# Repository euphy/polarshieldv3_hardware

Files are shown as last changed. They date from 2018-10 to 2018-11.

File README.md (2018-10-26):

View this project on [CADLAB.io](https://cadlab.io/project/1157). 

# polarshieldv3_hardware
Schematics, board and gerbers for Polarshield v3

Polarshield v3 is an aggregation board for connecting

* NodeMCU-32S
* 2x stepper drivers
* 320x240 LCD
* Touch panel
* SD card

v3.0e is the currently manufactured version that's inside recent PolargraphSD machines.

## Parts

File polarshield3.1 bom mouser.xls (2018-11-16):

POLARGRAPHSD V3.1 BOM
Mouser No | Mfr. No | Manufacturer | Customer No | Description | RoHS | Lifecycle | Order Qty. | Price (GBP) | Ext.: (GBP)
651-1770908 | 1770908 | Phoenix Contact |  | Fixed Terminal Blocks PTSM 0,5/ 4-2,5-H THR R32 | RoHS Compliant |  | 2 | £0.74 | £1.48
651-1778641 | 1778641 | Phoenix Contact |  | Pluggable Terminal Blocks PTSM 0,5/ 4-HH-2,5 THR R32 | RoHS Compliant |  | 4 | £0.695 | £2.78
651-1778858 | 1778858 | Phoenix Contact |  | Pluggable Terminal Blocks PTSM 0,5/ 4-P-2,5 | RoHS Compliant |  | 4 | £1.14 | £4.56
538-71764-0108 | 71764-0108 | Molex |  | Headers & Wire Housings RA BRKWY HEADER 8 PIN GOLD | RoHS Compliant |  | 1 | £0.97 | £0.97
710-865080345012 | 865080345012 | Wurth Electronics |  | Aluminium Electrolytic Capacitors - SMD WCAP-ASLI 16V 220uF 20% ESR=430mOhms | RoHS Compliant | New Product | 2 | £0.262 | £0.52
538-90121-0763 | 90121-0763 | Molex |  | Headers & Wire Housings 2.54MM CGRIDIII HDR 3P R/A SR SEL AU | RoHS Compliant |  | 1 | £0.595 | £0.60
863-BSS138LT1G | BSS138LT1G | ON Semiconductor |  | MOSFET 50V 200mA N-Channel | RoHS Compliant |  | 4 | £0.298 | £1.19
80-C0805C104Z3V | C0805C104Z3VACTU | KEMET |  | Multilayer Ceramic Capacitors MLCC - SMD/SMT 25volts 0.1uF Y5V -20+80% | RoHS Compliant |  | 2 | £0.076 | £0.15
652-CR0805FW1005ELF | CR0805-FW-1005ELF | Bourns |  | Thick Film Resistors - SMD Res 0805 10M 1% 125mW TC200 | RoHS Compliant By Exemption |  | 2 | £0.076 | £0.15
667-EEE-1CA101WP | EEE-1CA101WP | Panasonic |  | Aluminium Electrolytic Capacitors - SMD 100uF 16V | RoHS Compliant |  | 2 | £0.282 | £0.56
667-EXB-38V102JV | EXB-38V102JV | Panasonic |  | Resistor Networks & Arrays 1K OHM 5% | RoHS Compliant By Exemption |  | 1 | £0.092 | £0.09
667-EXB-38V103JV | EXB-38V103JV | Panasonic |  | Resistor Networks & Arrays 10K OHM 5% | RoHS Compliant By Exemption |  | 2 | £0.092 | £0.18
625-GF1A-E3 | GF1A-E3/67A | Vishay |  | Rectifiers 1.0 Amp 50 Volt | RoHS Compliant By Exemption |  | 1 | £0.329 | £0.33
720-LYR976-PS-36 | LY R976 | Osram Opto Semiconductor |  | Standard LEDs - SMD Yellow, 588nm 280mcd, 20mA | RoHS Compliant |  | 3 | £0.29 | £0.87
855-M20-7820442 | M20-7820442 | Harwin |  | Headers & Wire Housings 4 PIN SIL VERTICAL SOCKET GOLD+TIN | RoHS Compliant |  | 1 | £0.618 | £0.62
855-M20-7820842 | M20-7820842 | Harwin |  | Headers & Wire Housings 8 PIN SIL VERTICAL SOCKET GOLD+TIN | RoHS Compliant |  | 4 | £0.84 | £3.36
855-M20-7821446 | M20-7821446 | Harwin |  | Headers & Wire Housings 14 PIN SIL VERTICAL SOCKET TIN | RoHS Compliant |  | 1 | £1.10 | £1.10
855-M20-7822046 | M20-7822046 | Harwin |  | Headers & Wire Housings 20 PIN SIL VERTICAL SOCKET TIN | RoHS Compliant |  | 2 | £1.45 | £2.90
688-SKHHBY | SKHHBYA010 | ALPS |  | Tactile Switches 6.0x6.0x7.0mm 260gf | RoHS Compliant |  | 1 | £0.208 | £0.21

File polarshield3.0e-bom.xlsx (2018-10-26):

Part | Value | Device | Package | Description | MF | MPN | OC_FARNELL | OC_NEWARK | PROD_ID | SF_ID | VALUE | OPTIONAL
C1 | 100nF | C-EUC0805 | C0805 | CAPACITOR, European symbol
C2 | 100uF | CPOL-EU153CLV-0605 | 153CLV-0605 | POLARIZED CAPACITOR, European symbol
C3 | 100nF | C-EUC0805 | C0805 | CAPACITOR, European symbol
C4 | 220uF | CPOL-EU153CLV-0605 | 153CLV-0605 | POLARIZED CAPACITOR, European symbol
C5 | 100nF | C-EUC0805 | C0805 | CAPACITOR, European symbol
C6 | 220uF | CPOL-EU153CLV-0605 | 153CLV-0605 | POLARIZED CAPACITOR, European symbol
C7 | 100nF | C-EUC0805 | C0805 | CAPACITOR, European symbol
C8 | 100uF | CPOL-EU153CLV-0605 | 153CLV-0605 | POLARIZED CAPACITOR, European symbol
D1 | GF1A-E3/67A | DIODE-DO214BA | DO214BA | DIODE |  | GF1A-E3/67A
EXT_PWR |  | M02PTH | 1X02 | Standard 2-pin 0.1" header. Use with |  |  |  |  |  |  |  | OPTIONAL
JP3 | POWER_JACKPTH_LOCK | POWER_JACKPTH_LOCK | POWER_JACK_PTH_LOCK | Power Jack |  |  |  |  | CONN-08197 | PRT-00119
PWR |  | LEDCHIPLED_0805 | CHIPLED_0805 | LED
TX |  | LEDCHIPLED_0805 | CHIPLED_0805 | LED
RX |  | LEDCHIPLED_0805 | CHIPLED_0805 | LED
Q4 | BSS138 | MOSFET-NCHANNELSMD | SOT23-3 |  |  |  |  |  |  |  |  | OPTIONAL
Q5 | BSS138 | MOSFET-NCHANNELSMD | SOT23-3 |  |  |  |  |  |  |  |  | OPTIONAL
Q6 | BSS138 | MOSFET-NCHANNELSMD | SOT23-3 |  |  |  |  |  |  |  |  | OPTIONAL
Q7 | BSS138 | MOSFET-NCHANNELSMD | SOT23-3 |  |  |  |  |  |  |  |  | OPTIONAL
R1 | 1k | R-EU_M0805 | M0805 | RESISTOR, European symbol
R2 | 10k | R-EU_M0805 | M0805 | RESISTOR, European symbol
R4 | 1k | R-EU_M0805 | M0805 | RESISTOR, European symbol
R5 | 1k | R-EU_M0805 | M0805 | RESISTOR, European symbol
R8 | 1k | R-EU_M0805 | M0805 | RESISTOR, European symbol
R9 | 10k | R-EU_M0805 | M0805 | RESISTOR, European symbol
RESET | DTS-6 | DTS-6 | DTS-6 |  |  | SKHHBYA010
RN1 | 10k | 4R-NEXB38V | EXB38V | Array Chip Resistor |  |  | unknown | unknown |  |  |  | OPTIONAL
RN2 | 10k | 4R-NEXB38V | EXB38V | Array Chip Resistor |  |  | unknown | unknown |  |  |  | OPTIONAL
RN3 | 1k | 4R-NEXB38V | EXB38V | Array Chip Resistor |  |  | unknown | unknown
SERVO |  | PINHD-1X3/90 | 1X03/90 | PIN HEADER
U$2 | 2.4_TFT_SPI_TOUCH_SD | 2.4_TFT_SPI_TOUCH_SD | 2.4_TFT_SPI_TOUCH_SD
U$3 | MINI-360-MP2307 | MINI-360-MP2307 | MINI-360-MP2307
M1_CONN |  | PINHD-1X4/90 | 1X04/90 | PIN HEADER |  | 1778641
M2_CONN |  | PINHD-1X4/90 | 1X04/90 | PIN HEADER |  | 1778641
CN1 |  | DIP-BLACK-FEMALE-HEADER-VERT(8P-2.54) | H8-2.54 | 320030061 |  | F185-1108A1BSYC1 |  |  |  |  | 8p-2.54 | OPTIONAL
CN2 |  | DIP-BLACK-FEMALE-HEADER-VERT(8P-2.54) | H8-2.54 | 320030061 |  | F185-1108A1BSYC1 |  |  |  |  | 8p-2.54 | OPTIONAL
MOTOR_1 | A4988BREAKOUT | A4988BREAKOUT | A4988BREAKOUT
MOTOR_2 | A4988BREAKOUT | A4988BREAKOUT | A4988BREAKOUT
NODEMCU-32S1 | NODEMCU-32S | NODEMCU-32S | NODEMCU-32S

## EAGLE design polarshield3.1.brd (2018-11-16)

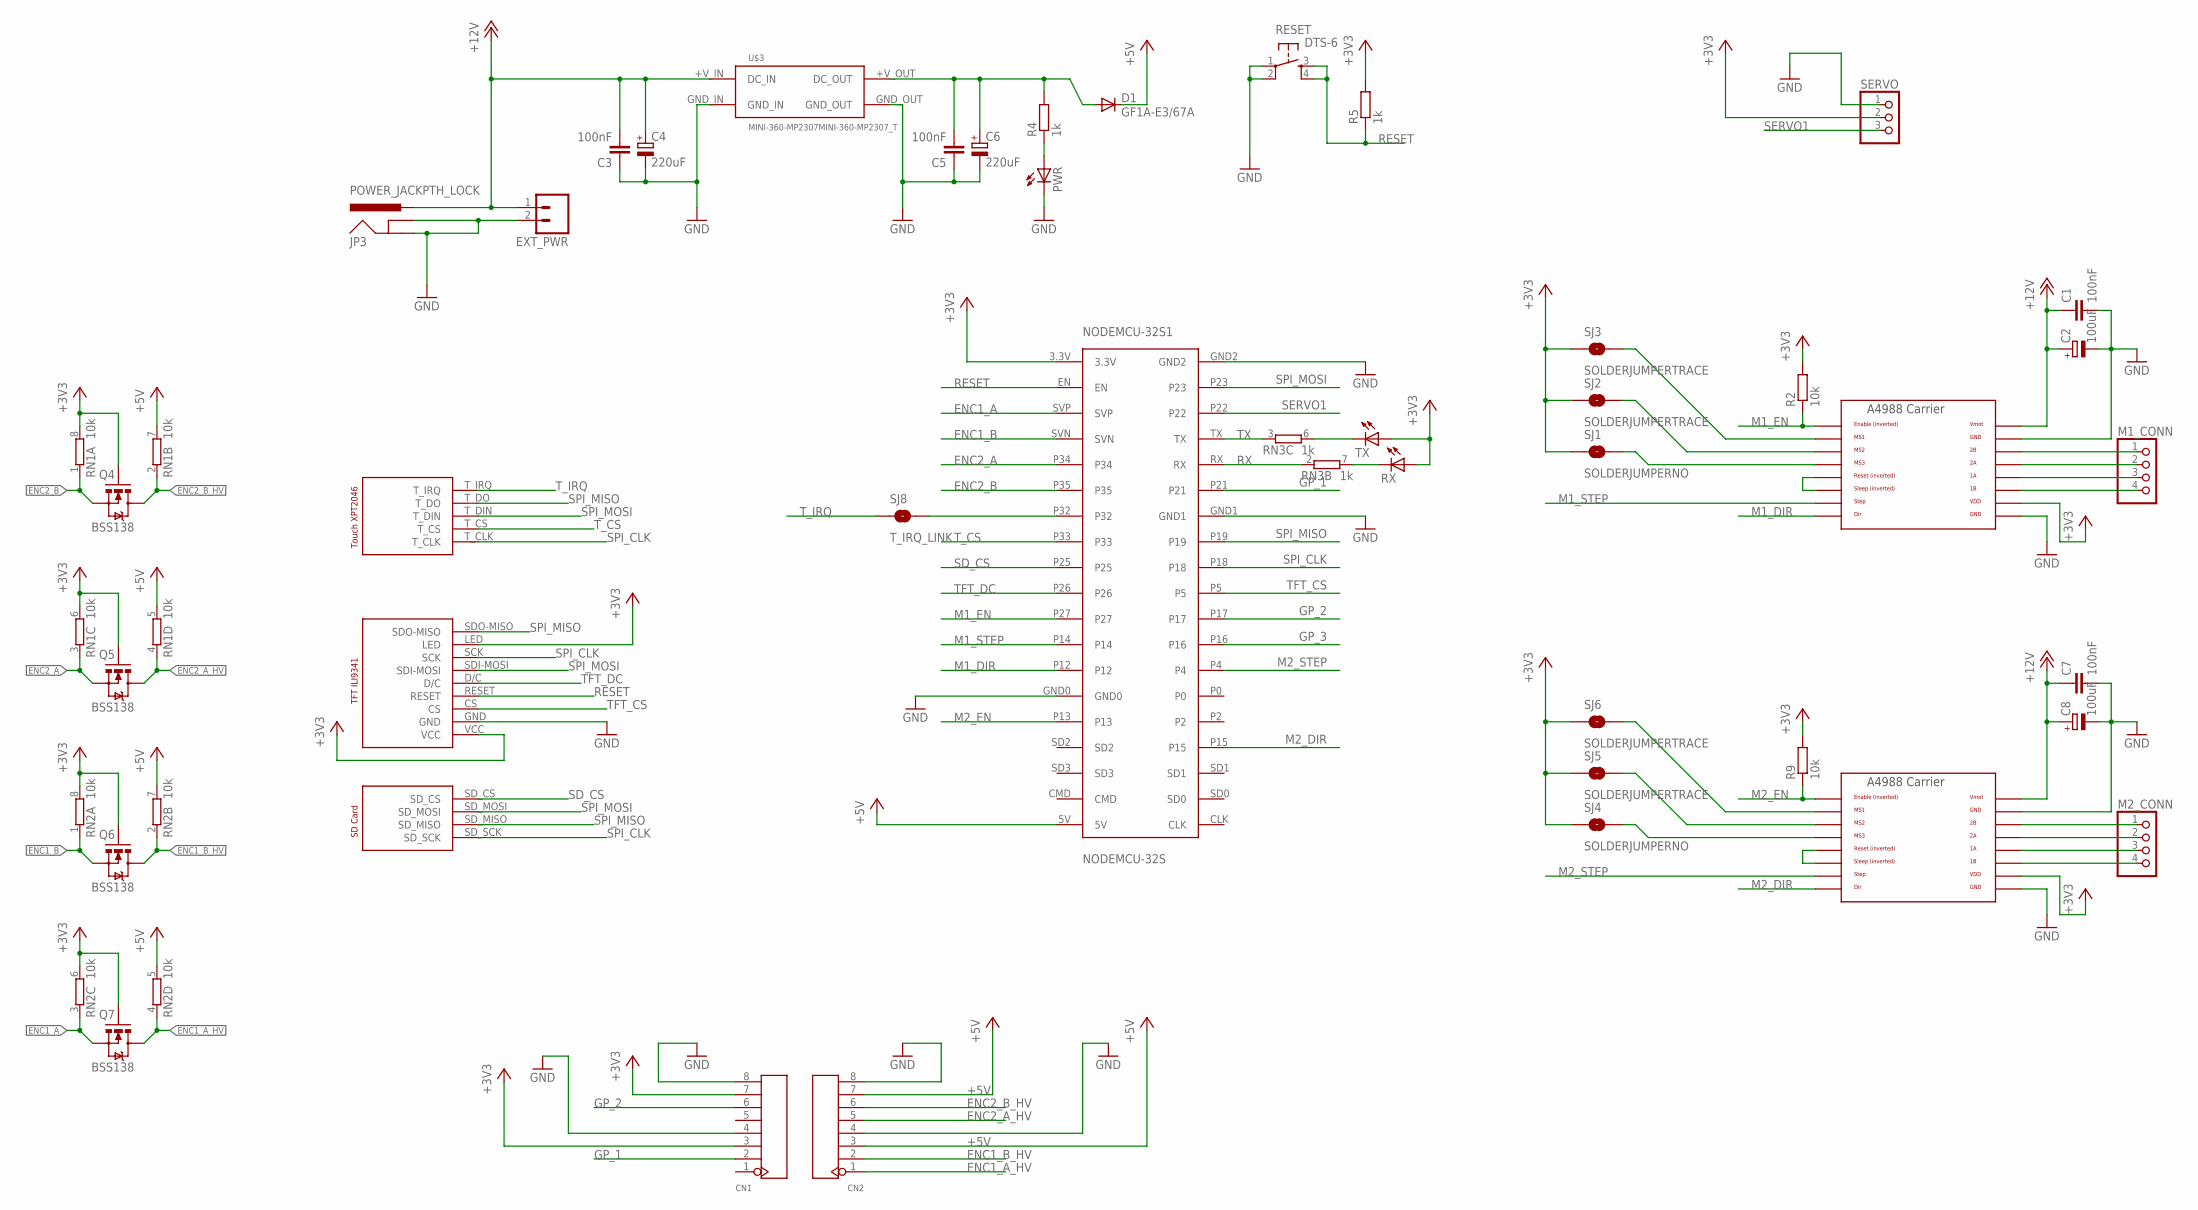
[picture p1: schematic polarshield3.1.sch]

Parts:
C1, C3, C5, C7: 100nF; C0805
C2, C8: 100uF; 153CLV-0605
C4, C6: 220uF; 153CLV-0605
CN1, CN2: DIP-BLACK-FEMALE-HEADER-VERT(8P-2.54); H8-2.54
D1: GF1A-E3/67A; DO214BA
EXT_PWR: M02PTH; 1X02
JP3: POWER_JACKPTH_LOCK; POWER_JACK_PTH_LOCK
M1_CONN, M2_CONN: PINHD-1X4/90; 1X04/90
MOTOR_1, MOTOR_2: A4988BREAKOUT
NODEMCU-32S1: NODEMCU-32S
PWR: LEDCHIPLED_0805; CHIPLED_0805
Q4, Q5, Q6, Q7: BSS138; SOT23-3
R2, R9: 10k; M0805
R4, R5: 1k; M0805
RESET: DTS-6
RN1, RN2: 10k; EXB38V
RN3: 1k; EXB38V
RX: LEDCHIPLED_0805; CHIPLED_0805
SERVO: PINHD-1X3/90; 1X03/90
SJ1, SJ4: SOLDERJUMPERNO; SJ_2S-NO
SJ2, SJ3, SJ5, SJ6: SOLDERJUMPERTRACE; SJ_2S-TRACE
SJ8: T_IRQ_LINK; SJ_2S-NO
TX: LEDCHIPLED_0805; CHIPLED_0805
U$2: 2.4_TFT_SPI_TOUCH_SD
U$3: MINI-360-MP2307MINI-360-MP2307_T; MINI-360-MP2307

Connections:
+3V3: CN1.3, CN1.7, MOTOR_1.VDD, MOTOR_2.VDD, NODEMCU-32S1.3.3V, Q4.1 (G), Q5.1 (G), Q6.1 (G), Q7.1 (G), R2.2, R5.2, R9.2, RN1.6 (2), RN1.8 (2), RN2.6 (2), RN2.8 (2), RX.A, SERVO.2, SJ1.1, SJ2.1, SJ3.1, SJ4.1, SJ5.1, SJ6.1, TX.A, U$2.LED, U$2.VCC
+5V: CN2.3, CN2.7, D1.C, NODEMCU-32S1.5V, RN1.5 (2), RN1.7 (2), RN2.5 (2), RN2.7 (2)
+12V: C1.1, C2.+, C3.2, C4.+, C7.1, C8.+, EXT_PWR.1, JP3.PWR, MOTOR_1.VMOT, MOTOR_2.VMOT, U$3.+V_IN (DC_IN)
ENC1_A: NODEMCU-32S1.SVP, Q7.2 (S), RN2.3 (1)
ENC1_A_HV: CN2.1, Q7.3 (D), RN2.4 (1)
ENC1_B: NODEMCU-32S1.SVN, Q6.2 (S), RN2.1
ENC1_B_HV: CN2.2, Q6.3 (D), RN2.2 (1)
ENC2_A: NODEMCU-32S1.P34, Q5.2 (S), RN1.3 (1)
ENC2_A_HV: CN2.5, Q5.3 (D), RN1.4 (1)
ENC2_B: NODEMCU-32S1.P35, Q4.2 (S), RN1.1
ENC2_B_HV: CN2.6, Q4.3 (D), RN1.2 (1)
GND: C1.2, C2.-, C3.1, C4.-, C5.1, C6.-, C7.2, C8.-, CN1.4, CN1.8, CN2.4, CN2.8, EXT_PWR.2, JP3.GND, JP3.GNDBREAK, MOTOR_1.GND, MOTOR_1.GND@0 (GND), MOTOR_2.GND, MOTOR_2.GND@0 (GND), NODEMCU-32S1.GND0, NODEMCU-32S1.GND1, NODEMCU-32S1.GND2, PWR.C, RESET.1, RESET.2, SERVO.1, U$2.GND, U$3.GND_IN, U$3.GND_OUT
GP_1: CN1.2, NODEMCU-32S1.P21
GP_2: CN1.6, NODEMCU-32S1.P17
GP_3: NODEMCU-32S1.P16
M1_DIR: MOTOR_1.DIR, NODEMCU-32S1.P12
M1_EN: MOTOR_1.EN, NODEMCU-32S1.P27, R2.1
M1_STEP: MOTOR_1.STEP, NODEMCU-32S1.P14
M2_DIR: MOTOR_2.DIR, NODEMCU-32S1.P15
M2_EN: MOTOR_2.EN, NODEMCU-32S1.P13, R9.1
M2_STEP: MOTOR_2.STEP, NODEMCU-32S1.P4
unnamed: NODEMCU-32S1.P32, SJ8.2
unnamed: MOTOR_1.RST, MOTOR_1.SLP (SLEEP)
unnamed: MOTOR_1.MS3, SJ1.2
unnamed: MOTOR_1.MS2, SJ2.2
unnamed: MOTOR_1.MS1, SJ3.2
unnamed: C5.2, C6.+, D1.A, R4.2, U$3.+V_OUT (DC_OUT)
unnamed: PWR.A, R4.1
unnamed: MOTOR_2.MS3, SJ4.2
unnamed: M1_CONN.1, MOTOR_1.2B
unnamed: M1_CONN.2, MOTOR_1.2A
unnamed: M1_CONN.3, MOTOR_1.1A
unnamed: M1_CONN.4, MOTOR_1.1B
unnamed: RN3.6 (2), TX.C
unnamed: RN3.7 (2), RX.C
unnamed: MOTOR_2.MS2, SJ5.2
unnamed: MOTOR_2.MS1, SJ6.2
unnamed: MOTOR_2.RST, MOTOR_2.SLP (SLEEP)
unnamed: M2_CONN.1, MOTOR_2.2B
unnamed: M2_CONN.2, MOTOR_2.2A
unnamed: M2_CONN.3, MOTOR_2.1A
unnamed: M2_CONN.4, MOTOR_2.1B
RESET: NODEMCU-32S1.EN, R5.1, RESET.3, RESET.4, U$2.RESET
RX: NODEMCU-32S1.RX, RN3.2 (1)
SD_CS: NODEMCU-32S1.P25, U$2.SD_CS
SERVO1: NODEMCU-32S1.P22, SERVO.3
SPI_CLK: NODEMCU-32S1.P18, U$2.SCK, U$2.SD_SCK, U$2.T_CLK
SPI_MISO: NODEMCU-32S1.P19, U$2.SDO-MISO, U$2.SD_MISO, U$2.T_DO
SPI_MOSI: NODEMCU-32S1.P23, U$2.SDI-MOSI, U$2.SD_MOSI, U$2.T_DIN
TFT_CS: NODEMCU-32S1.P5, U$2.CS
TFT_DC: NODEMCU-32S1.P26, U$2.D/C
TX: NODEMCU-32S1.TX, RN3.3 (1)
T_CS: NODEMCU-32S1.P33, U$2.T_CS
T_IRQ: SJ8.1, U$2.T_IRQ

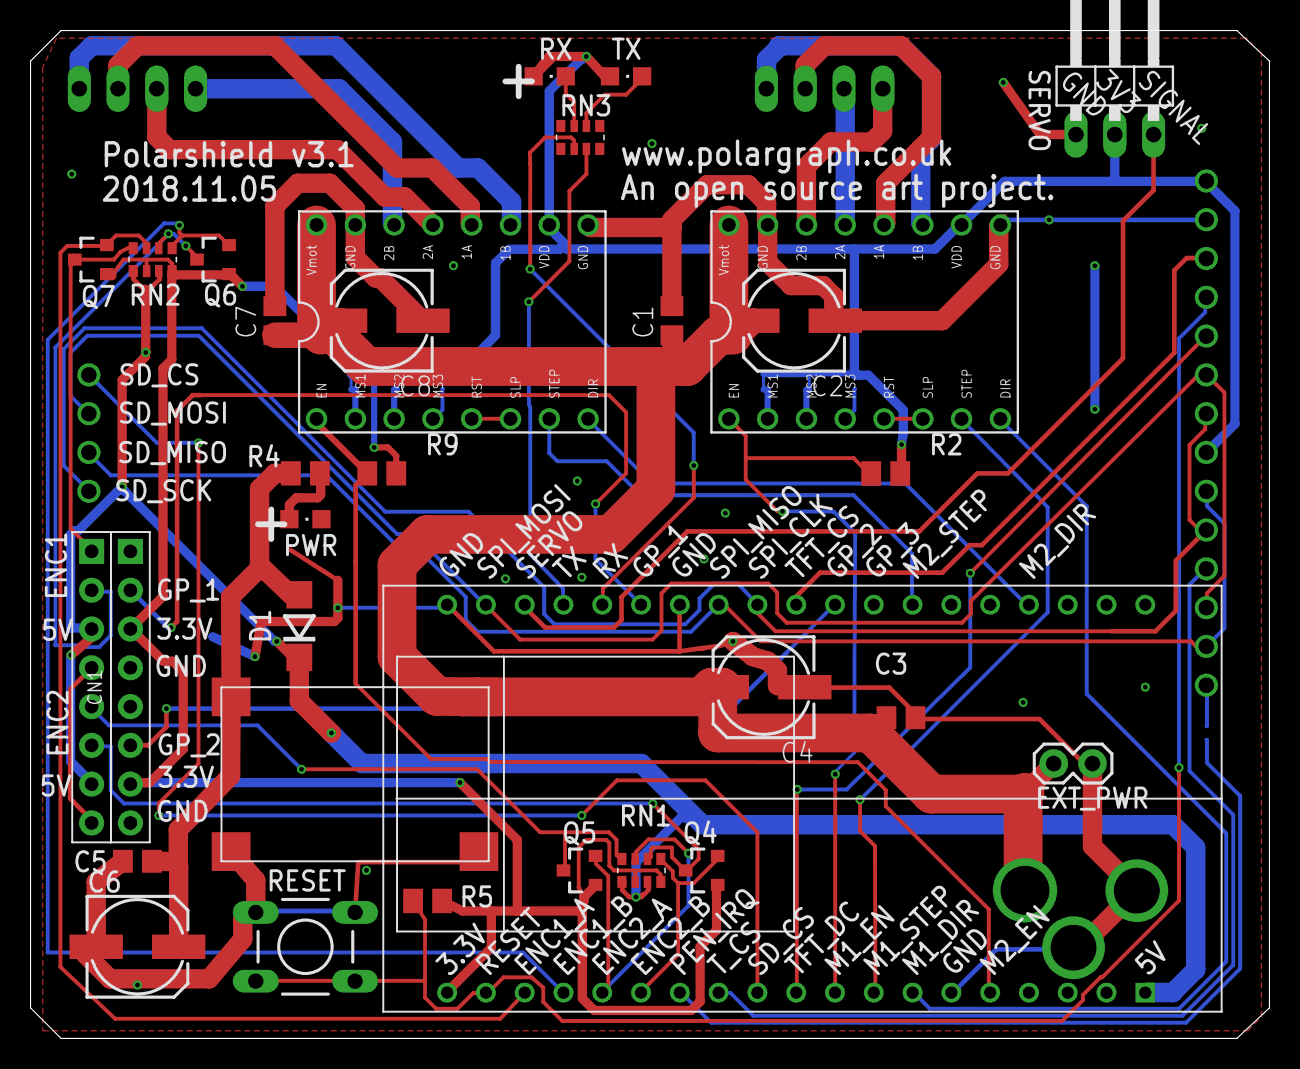
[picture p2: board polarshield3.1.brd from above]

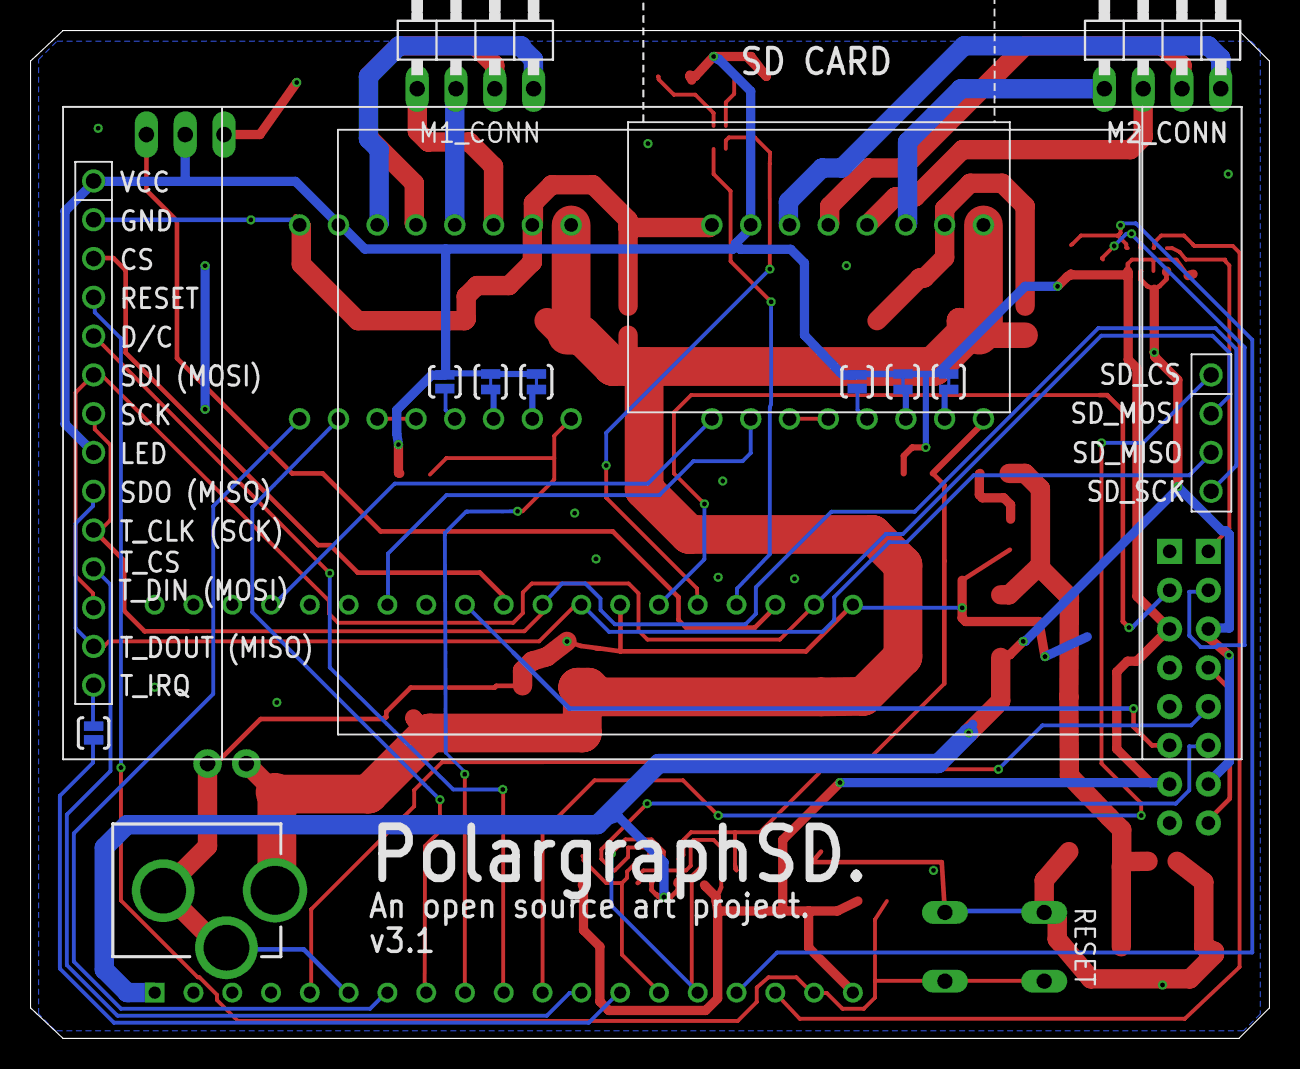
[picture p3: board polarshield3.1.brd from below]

Board: 2 copper layers, 81.1 x 66.0 mm, 43 parts (11 on the bottom side), 53 nets.

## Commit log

2018-04-15 Initial files
    [polarshield3.0.brd, polarshield3.0.sch]
2018-04-22 first version looks ok visually
    [polarshield3.0.brd, polarshield3.0.sch]
2018-04-22 Built gerbers
    [polarshield3.0.GBL, polarshield3.0.GBO, polarshield3.0.GBP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]
2018-06-10 Minor changes based on first board.
    [polarshield3-bom.xlsx, polarshield3.0b.sch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]
2018-06-10 Gerbers for v3.0e
    [polarshield3.0b.brd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]
2018-06-11 v3.0e rebuilt
    [polarshield3.0e.brd, polarshield3.0e.sch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]
2018-10-02 3.0f removed 100k resistor from MS1 pin.
    [polarshield3.0f.brd, polarshield3.0f.sch]
2018-10-26 Added part number GF1A-E3/67A to D1, #1
    [polarshield3-bom.xlsx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]
2018-10-26 Added bom, closes #1
    [polarshield3.0e-bom.xlsx]
2018-11-03 v3.0f. Removed 1k resistors, moved motor connectors and pads for mini-360.
    [polarshield3.0f.brd, polarshield3.0f.sch]
2018-11-03 v3.1 changed servo supply voltage to 3.3v
    [polarshield3.0f.brd, polarshield3.0f.sch]
2018-11-16 v3.1 - replaced 5v servo power supply with 3.3v
    [polarshield3.1.GBL, polarshield3.1.GBO, polarshield3.1.GBP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]
2018-11-16 adding mouser bom
    [polarshield3.1 bom mouser.xls]

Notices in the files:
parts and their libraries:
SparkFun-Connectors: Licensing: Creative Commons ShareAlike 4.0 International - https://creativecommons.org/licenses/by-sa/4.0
